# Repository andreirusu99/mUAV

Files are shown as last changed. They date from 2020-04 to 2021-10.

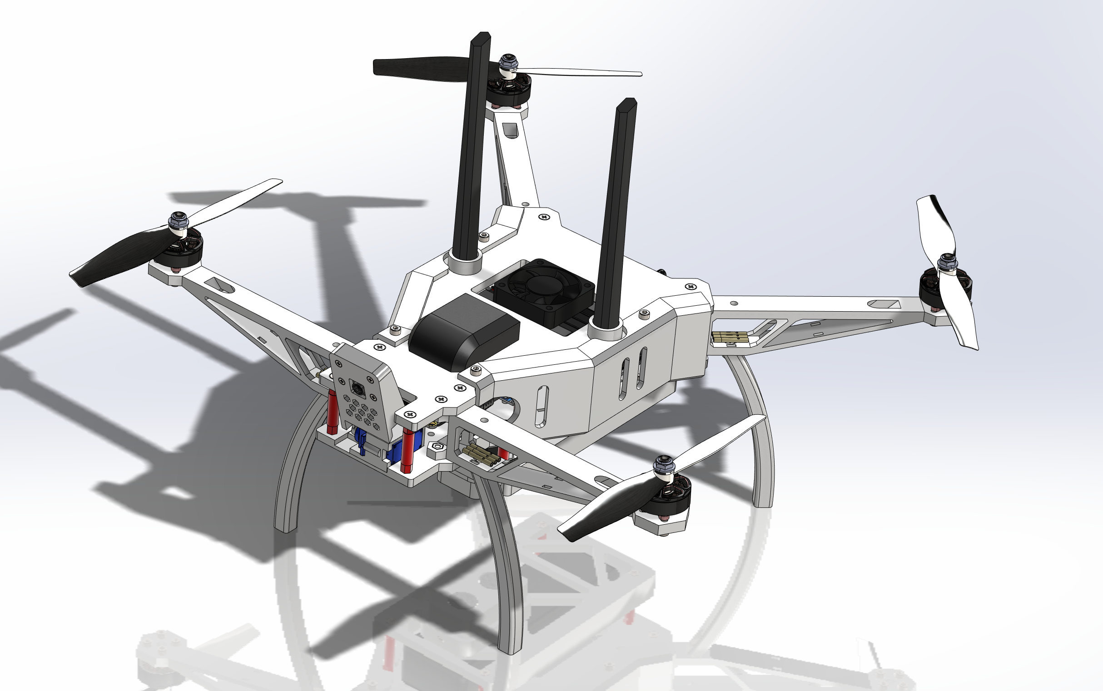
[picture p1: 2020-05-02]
Hardware/cad.png

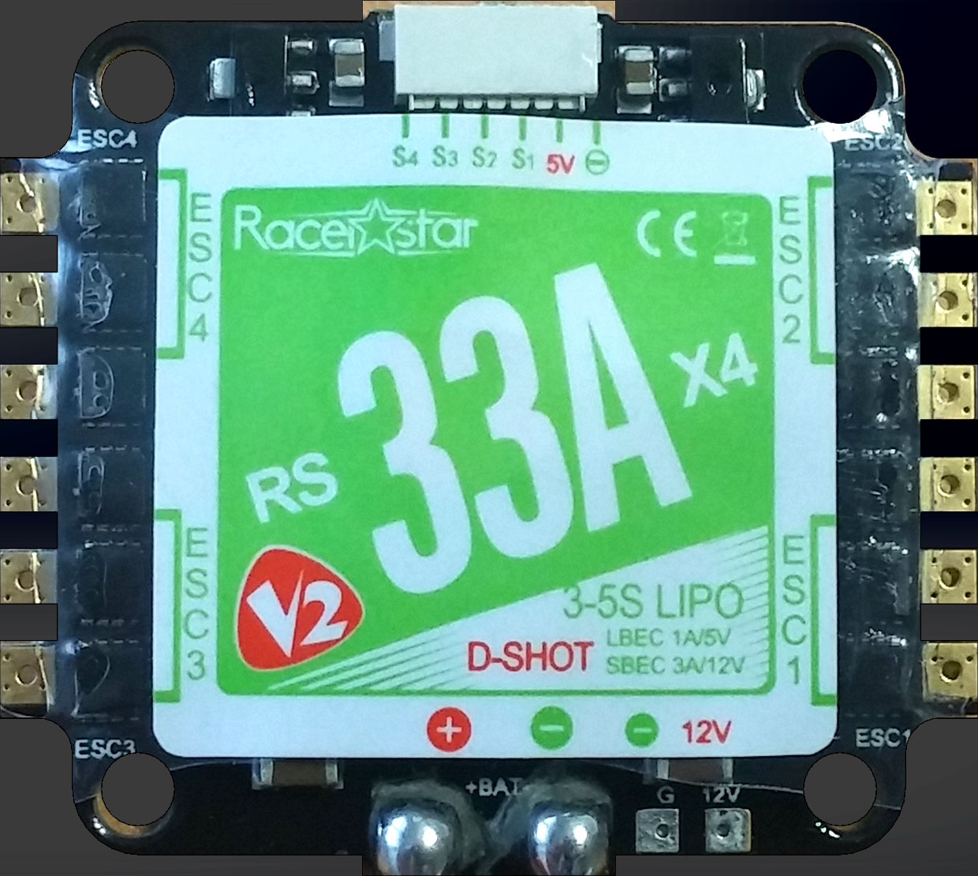
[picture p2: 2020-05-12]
Hardware/esc-racerstar-4in1-33a-v2-1.snapshot.1/TEXT_RACERSTAR_33A_TOP.jpg

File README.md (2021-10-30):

### ***This project represents the work for my bachelor's thesis and therefore, any commercial usage or distribution of the files without expressly granted written permission and consent is prohibited.***

Complete information in the [Thesis](/Thesis.pdf) document and the presentation (_Crowd identification and monitoring using UAVs.pdf_)

## Summary
Edge computing system for mUAV crowd identification and monitoring, complete with client application, real-time dashboard and statistics.

The purpouse of the project is to implement a crowd identification and monitoring system that runs on edge, on a drone that I designed and built (see *Hardware* folder for details).

Edge computing is done on a nVIDIA Jetson Nano Dev Kit installed on the quadcopter, that runs a ROS environment.

Crowd monitoring is performed using neural networks designed for edge devices (SSD MobileNet V2) and computer vision frameworks such as OpenCV.

The Jetson communicates completely wireless over a Wi-Fi hotspot from a computer (my laptop).

## Frameworks & APIs
- **ROS Melodic** (Robot Operating System), Python implementation
- **OpenCV 4.1.1**, built from source with CUDA support
- **TensorFlow 2**, for model tests
- **Flask Server**, for live video streaming
- **ReactJS**, for the front-end application
- **GoogleMapsAPI** for real-time GPS localization
- **ROSLibJS** for remote ROS topic access
- **YAMSPy** for MSP communication with the FC

## Folder Structure
### [catkin_ws](/catkin_ws)
Contains the ROS workspace, which constitutes the main functional part of the system. Inside, there are the source files of ROS Nodes, message definitions, and a launch file that launches all the required nodes. The programming language is Python, using the *rospy* library.

### [ros_client](/ros_client)
Contains a React application that uses ROSLibJS to interact with the Master Node running on the Jetson Nano, that displays real-time data in a dashboard by accessing the topics of the ROS runtime. 

### [GroundStation](/GroundStation)
Contains a Python script used to send UDP commands over Wi-Fi from a joystick connected to the ground computer (my laptop). The commands are sent as-is and all processing and interpretation of these commands is done in the air on the Jetson.
> Note: the drone's flight is not automated, therefore an operator is required for flying (flight automation was outside the scope of this project).

### [Hardware](/Hardware)
Contains the 3D models that make up the quadcopter. These parts were designed with 3D printing manufacturing in mind, and as such, are only suitable for this kind of manufacturing process. The parts were printed on my own 3D printer using PETG. and PLA. A detailed description of all the hardware components used (boards, sensors, actuators) is found in the Readme file inside the folder.

### [ModelTest](/ModelTest)
Is a folder that I created to host my neural network experiments, until I decied for the final implementation that I would transfer over to the Jetson for inferencing.

### Further information can be found in each respective folder.

## Helpful work by others
 - [DronePilot](https://github.com/alduxvm/DronePilot) - UDP joystick communication between computers
 - [YAMSPy](https://github.com/thecognifly/YAMSPy) - MSP library for Python
 - [Jetson Inference](https://github.com/dusty-nv/jetson-inference) - official deep learning inference library from nVidia

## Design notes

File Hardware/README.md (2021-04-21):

# Hardware

## Quadcopter
Designed with 3D printing and modularity in mind, it acts as an enclosure for all the other components. 
Designed in SolidWorks and sliced with Ultimaker Cura.

It features a 3-deck design, where in the middle deck lie the most important components (Jetson Nano, Flight Controller, Camera). 
The upper deck hosts the GPS and the Wi-Fi antennas, while the lower deck contains the LiPo battery, the sonar, and a servo release mechanism.

The front arms are pulled back (in comparison to a regular simmetrical quadcopter) in order for them not to interfere with the camera's image. The propellers are placed well above the center of gravity for increased stability.
Additionally, each motor is inclined by 3 degrees horizontally to further improve hover stability.

The entire craft is suspended on 4 independent legs that can be easily replaced.
The motor arms are also modular and can be easily replaced if broken.
The sides are covered for extra protection in case of falls.

Drone

## Main Computer
The nVidia Jetson Nano Developer Kit is used in this project, mainly due to the fact that it boasts a Maxwell GPU (alongside a 4 core ARM CPU) capable of fast deep-learning inference speeds.
Additionally, the wealth of expasion ports and headers helps in connecting sensors and building complex applications. 
The Jetson is improved by the addition of an Intel Wi-Fi card, in the dedicated E key slot under the Nano module. 
This card has 2 antennas, which come out of the top of the drone and give the nano very good wireless coverage.

Runs Tegra4Linux, a custom Linux distro specific to the Jetson platform.

Jetson Nano

## Flight Controller
This is the component that directly interacts with the motors. The FC contains 4 separates ESCs to control the 4 separate motors.
It also provides a pass-through interface to control the servo to which the camera is attached, for tilt action.
It receives MSP (MultiWii Serial Protocol) commands on separate channels and runs PID loops and stabilisation algorithms to keep the drone level.
Uses Betaflight firmware and has an integrated IMU with an accelerometer and gyroscope.
It is mounted in the head of the craft, behind the camera and the tilting servo.

Flight Controller

## Sensors

### Camera
The camera used in this project is the RasberryPi Camera V2, with up to 4K resolution at 30FPS. It gives out a decent image, and has very good support on the Jetson Nano.
It plugs into one of the CSI camera ports on the Jetson.

RPi Cam V2

### Sonar
I used a simple HC-SR04(P) ultrasonic sensor as a sonar to obtain altitude information. It is mounted on the underside of the craft, facing downwards.

Sonar

### Barometer
A Bosch BMP-280 barometric and temperature sensor is used for altitude information when the craft is out of the range of the sonar (about 4m from the ground).
Communication between it and the Jetson is done using I2C. It is mounted behind the FC, above a 5V power regulator.

BMP-280

### GPS
As GPS, a VK-162 is used. It provides simple USB interface access and has good accuracy and reliability. 
It can be seen mounted on the topmost part of the drone, for better location signal.

VK-162

## Actuators
### Camera tilt servo
The camera is mounted on a servo arm that allows its tilting from 0 to 90 degrees. This is a helpful feature to have when taking shots from above, and is commonly found on cinematic drones (although those have extra axes).

Servo tilt

### Servo release mechaism
Additionally, a servo release mechanism is mounted on the underside of the craft, next to the sonar. It allows the carrying of objects, with a theoretical max capacity of about 2kg, but this is not tested.
> Note: this feature is not used in the project, I might do something with it afterwards

Servo release

### Motors and Propellers
I used 4 Turnigy BLDC, 2600KV motors (common for medium-scale drones), together with 6040 propellers (6" long, 4" pitch), with a rated thrust of 800g each.

## Stats
- Mass without battery: **~850g**
- Mass with battery: **~1200g** (3S LiPo 5200mAh, 55Wh)
- Propeller span: **50cm**
- Height: **15cm** (without antennas)
- Power consumption: **~10W** idle, **~150W** hover + **~10W** JetsonNano
- Average flight time: **20 min**
> Power consumption and flight times depend heavily on external factors such as air temperature, wind, humidity.

## Extra Photos
### Top View
> Shows the upper deck, with the Jetson Nano's fan, the GPS module, the antennas and various other design elements

top

### Bottom View
> Shos the sonar, the servo release, and the battery cage.

bottom

### Back View
> Shows the I/O ports of the Jetson. Left USB is the Flight Controller, right USB is the GPS.

back

### Flight Controller and Camera Servo
> You can spot the ventilation cutouts and the M3 nut capture locations embedded in the 3D-printed plastic

front

### Internal View
> Not all components had been installed when this picture was taken.

internal

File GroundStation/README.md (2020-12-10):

# GroundStation

### Contains a single Python script used to stream joystick data to the Jetson Nano over an UDP WebSocket.

## Flow

- reads the joystick axes and buttons using the `pygame` library
- rounds the axes to 3 decimals
- sends the data using an UDP socket (`socket.SOCK_DGRAM`) 

#### The UDP send address (IP and Port) are configured to be on the local network of the Wi-Fi hotspot created by the laptop.

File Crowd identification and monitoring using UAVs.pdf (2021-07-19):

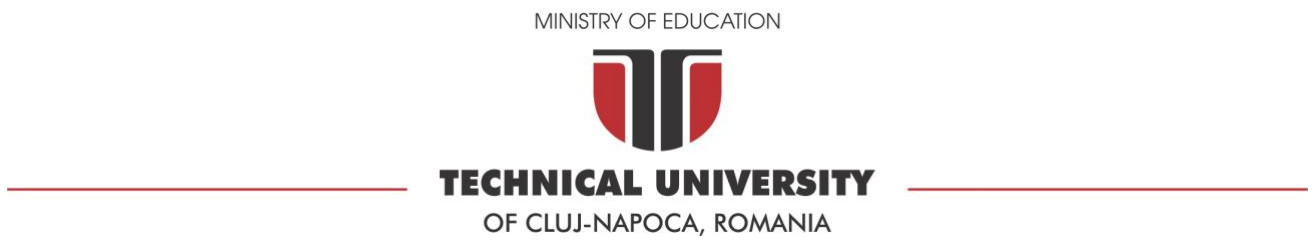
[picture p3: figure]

# Real-time crowd identification and monitoring using UAVs

# Student: Andrei Rusu

# Coordinator: Prof. Dr. Radu Dănescu

Technical University of Cluj-Napoca, Computer Science Department | 1

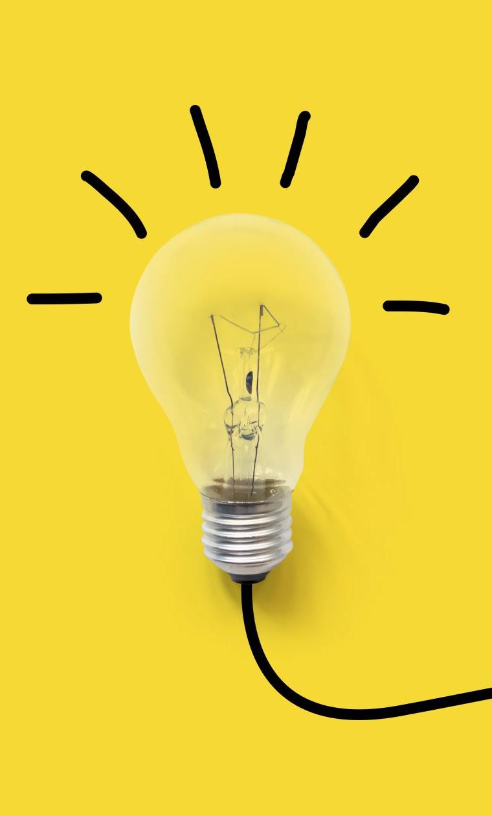
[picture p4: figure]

# Problem

# - Crowds in public places = large health hazard

# - Difficult to enforce social distancing

# - Traditional methods are slow and require offsite processing

Technical University of Cluj-Napoca, Computer Science Department | 2

# Objectives

# - Implement CV method for estimating overcrowding & social distancing

# - Leverage edge computing to enable real-time processing

# - Use UAVs for fast deployment anywhere

Technical University of Cluj-Napoca, Computer Science Department | 3

# Proposed solution

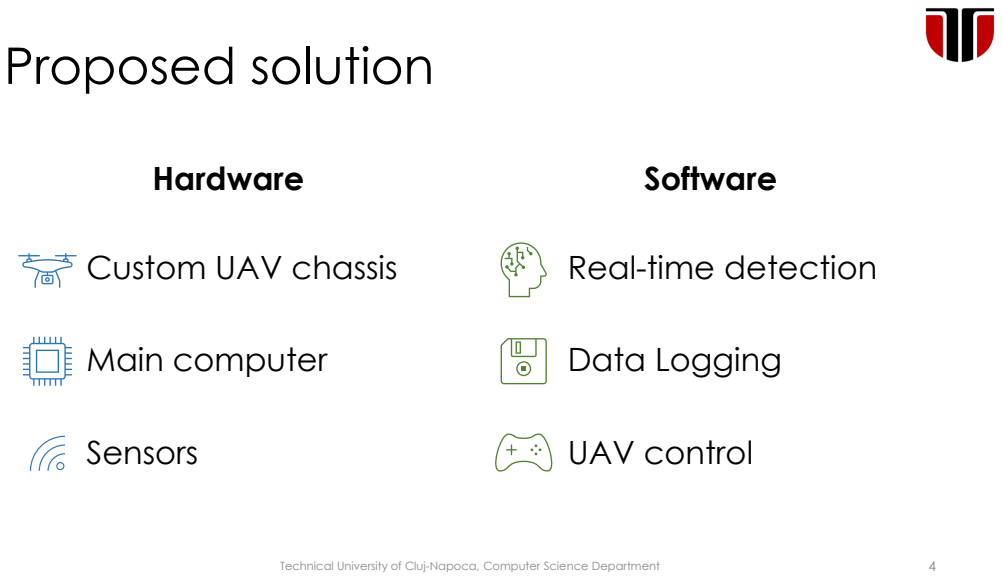
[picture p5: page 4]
Hardware; Main computer; Sensors; Software; Data Logging; UAV control; Technical University of Cluj-Napoca, Computer Science Department

Custom UAV chassis

Real-time detection

# Hardware platform

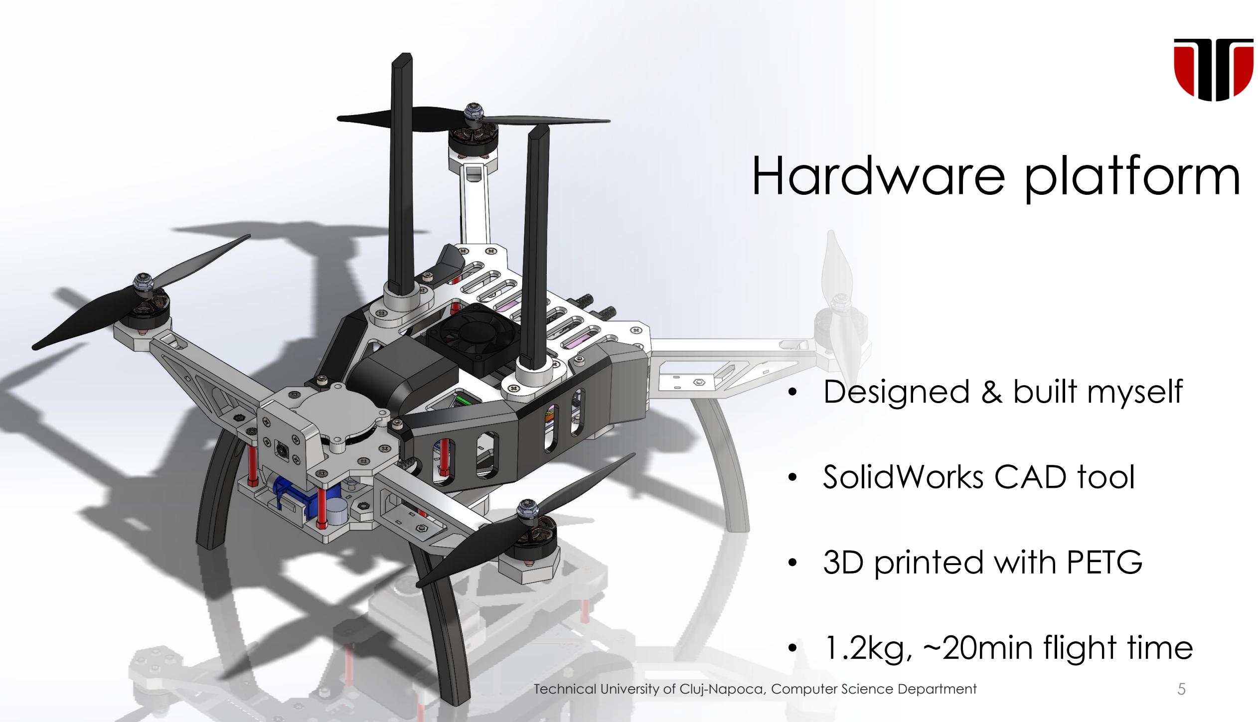
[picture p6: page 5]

# - Designed & built myself

# - SolidWorks CAD tool

# - 3D printed with PETG

# - 1.2kg, ~20min flight time

Technical University of Cluj-Napoca, Computer Science Department | 5

# Designed assemblies

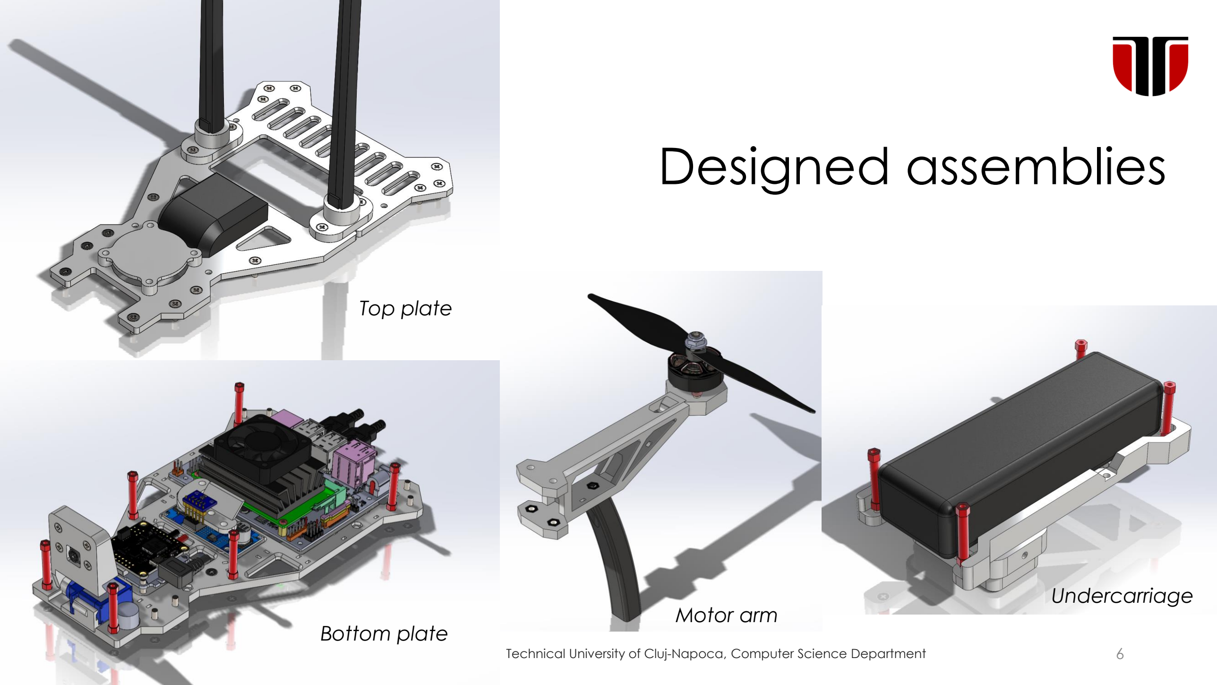
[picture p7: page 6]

## Bottom plate

## Top plate

## Motor arm

## Undercarriage

Technical University of Cluj-Napoca, Computer Science Department | 6

# Hardware components

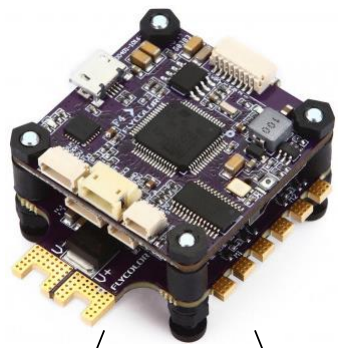
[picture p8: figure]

7

x4

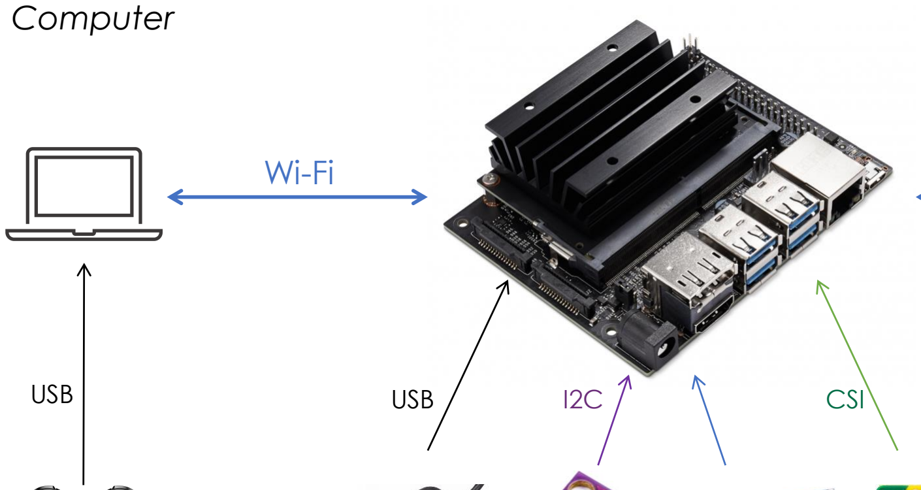
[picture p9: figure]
USB; CSI; Computer

GPS | Barometer | Sonar | Camera | Servo | Motors

# MSP

PWM | PWM

# Ground Station

NVidia Jetson Nano | Flight Controller

## Gamepad

Technical University of Cluj-Napoca, Computer Science Department

# Software components

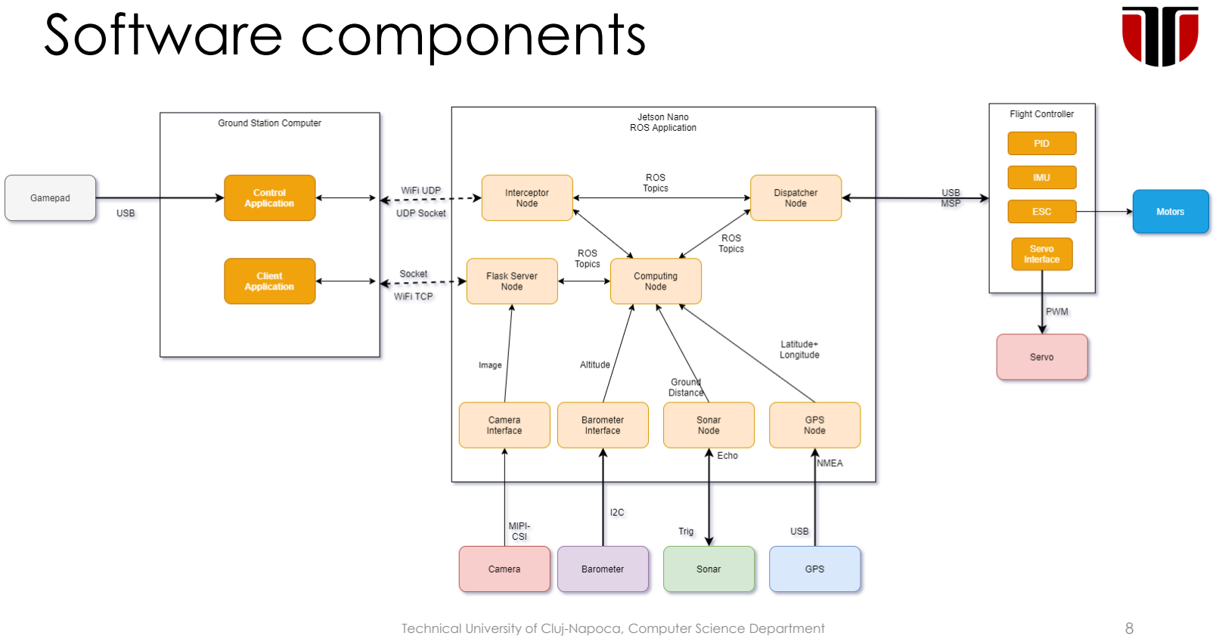
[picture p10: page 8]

Technical University of Cluj-Napoca, Computer Science Department | 8

# Application

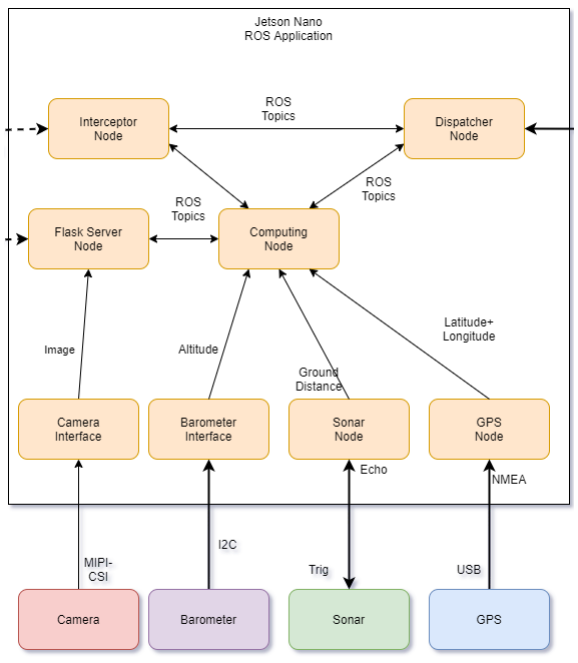
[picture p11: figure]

Technical University of Cluj-Napoca, Computer Science Department | 9

# - MobileNetV2 SSD for person detection

# - Overcrowding & social distancing

# - Data gathering & logging to .csv

# - Flight control via MSP

# Parallel execution

## runs on JetsonNano

# Person detection

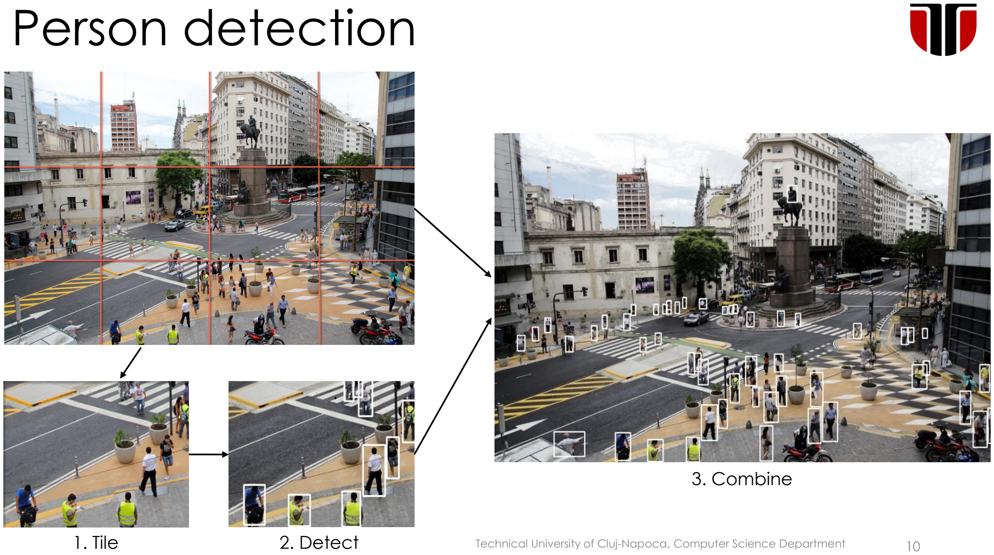
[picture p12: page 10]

1. Tile | 2. Detect | Technical University of Cluj-Napoca, Computer Science Department | 10

## 3. Combine

Technical University of Cluj-Napoca, Computer Science Department | 11

# - Density = Area / People

# - Obtain area of ground projection from H and αcam

# - Pixel size = Area / resolution [cm]

# - Distance on ground = Distance on image * pixel size

# Overcrowding & Social distancing

# Estimate distances between people

# Estimate average density of crowd

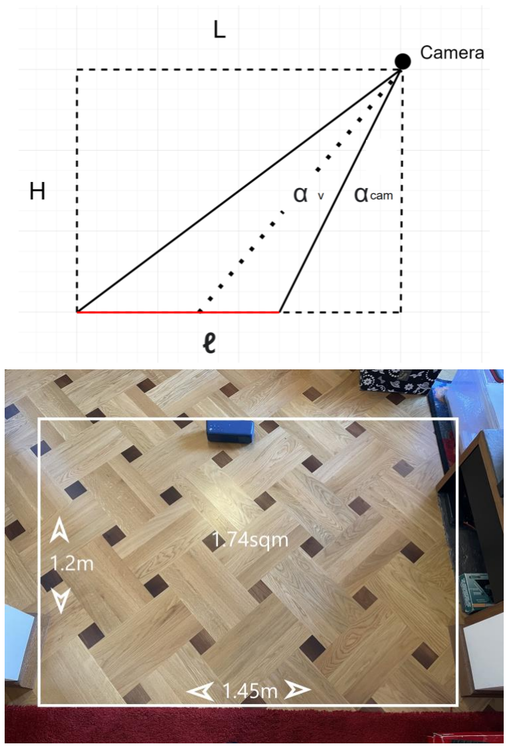
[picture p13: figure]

## Area estimation test

# Client Application

## runs on GS Computer

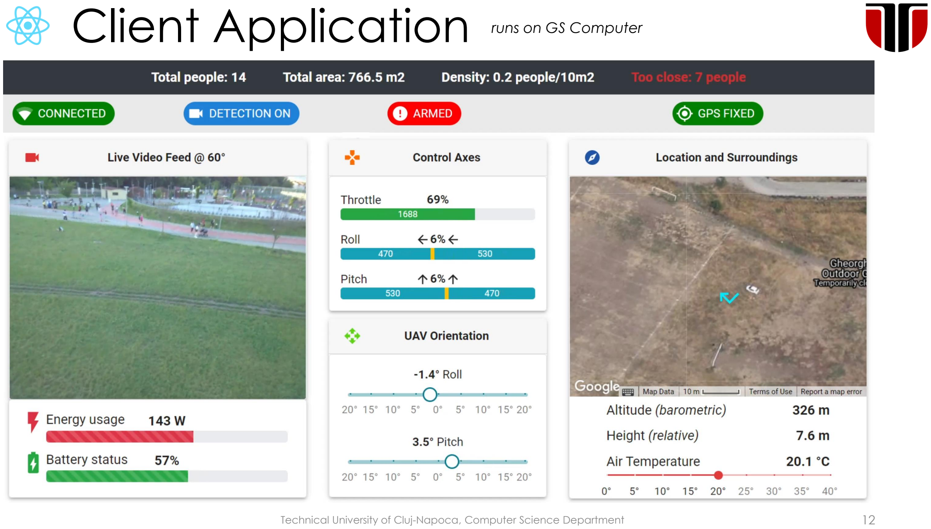
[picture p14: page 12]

Technical University of Cluj-Napoca, Computer Science Department | 12

# Control application

# - Sends UDP messages to the ROS application

# - Message:

# 4 control axes (Roll, Pitch, Throttle, Yaw) 2 triggers 6 buttons 1 Directional pad

# - Controls drone & functions

## (flying, camera tilt, detection etc.)

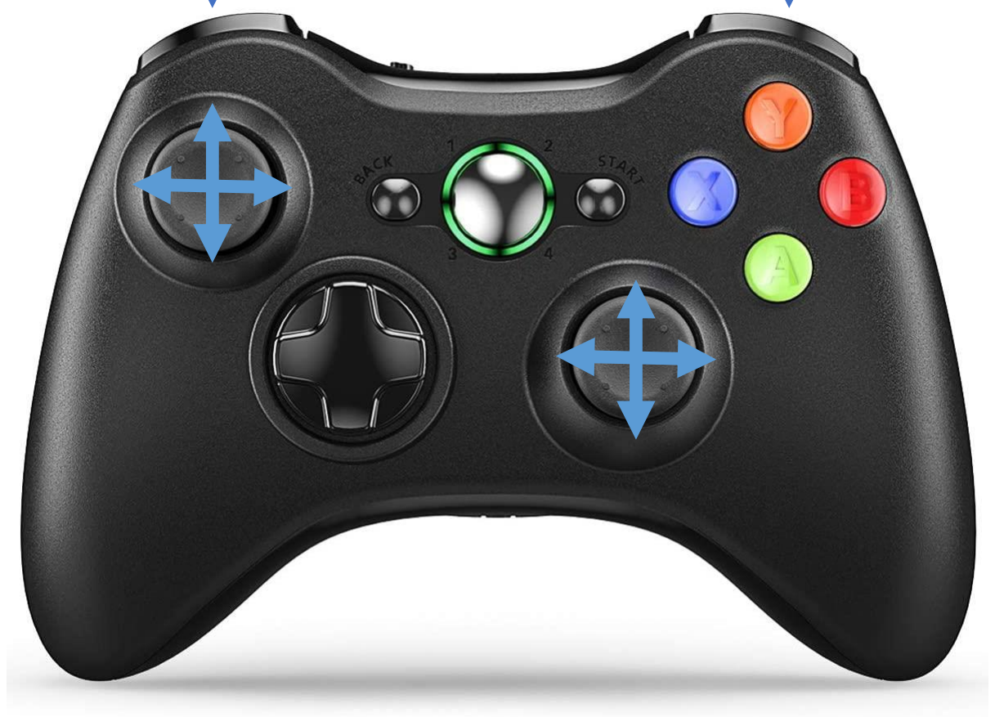
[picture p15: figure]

Technical University of Cluj-Napoca, Computer Science Department | 13

## runs on GS computer

# Validation

Board | CPU | TOPS | Interfaces | Speed | Weight | Cost | PricePerf
RPi4 | 4 | 0 | USB2+3,HDMI, UART, I2C, SPI | 483ms | 46g | $50 | 24,150
RPi4 + Coral | 4 | 4 | USB2+3, UART, I2C, SPI | 25ms | ~100g | $110 | 2750
Nano Jetson | 4 | 0.5 | USB3, DP, HDMI, UART, I2C, SPI | 25ms | 250g | $100 | 2500
Xavier Jetson | 6 | 21 | UART, I2C, SPI USB3, DP, HDMI, | 1.25ms | 400g | $400 | 500
Technical University of Cluj-Napoca, Computer Science Department | 14
N | M | Tile Width | Tile Height | Runtime/Tile | Runtime/Image | Correctness
3 | 2 | 544 | 616 | 50ms | 305ms | 65%
4 | 3 | 408 | 410 | 54ms | 650ms | 67%
5 | 4 | 326 | 308 | 45ms | 905ms | 73%
6 | 4 | 272 | 308 | 43ms | 1050ms | 76%
8 | 6 | 204 | 205 | 44ms | 2100ms | 67%

# Main computer comparison using MobileNetV2SSD inference speed

# Image tiling comparison for 1632x1232 input image

# Results

## Flight deployment at Baza Sportivă Gheorgheni

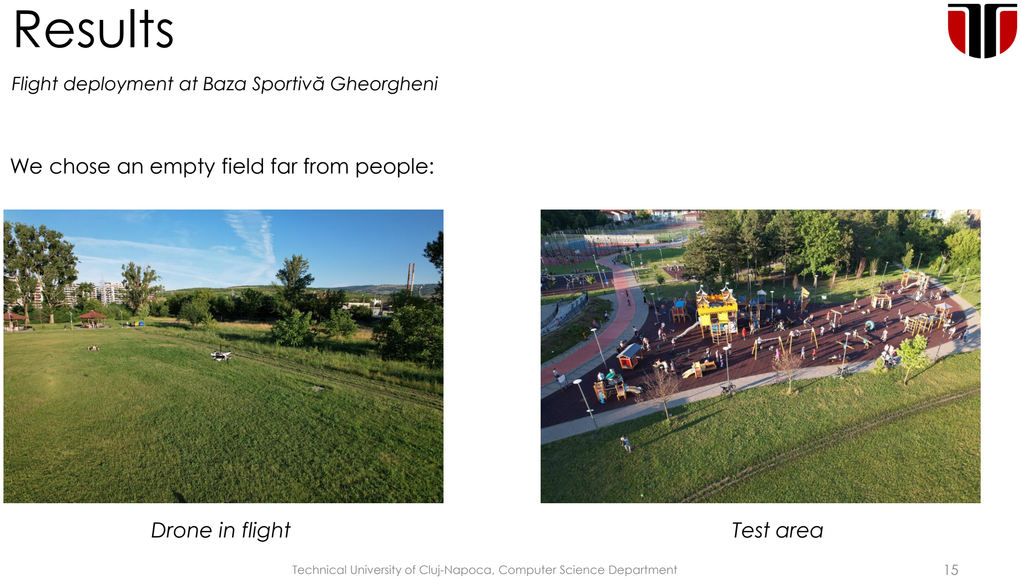
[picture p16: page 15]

Technical University of Cluj-Napoca, Computer Science Department | 15

# Drone in flight

# Test area

# We chose an empty field far from people:

# Results

16

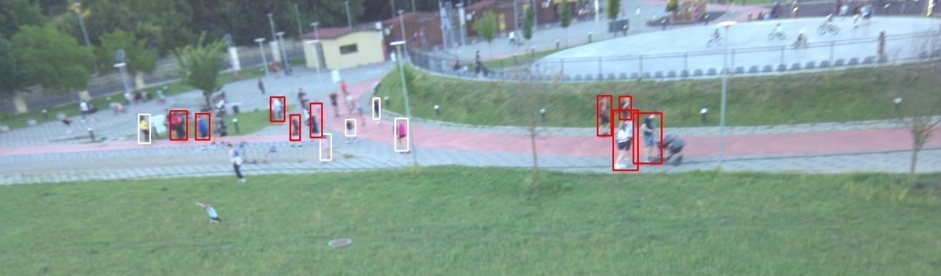
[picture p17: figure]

# 7.7m high, 60deg camera angle

# 14 of 23 people detected (60.8%)

# 9 too close, 0.18/10m2 density in 1340m2

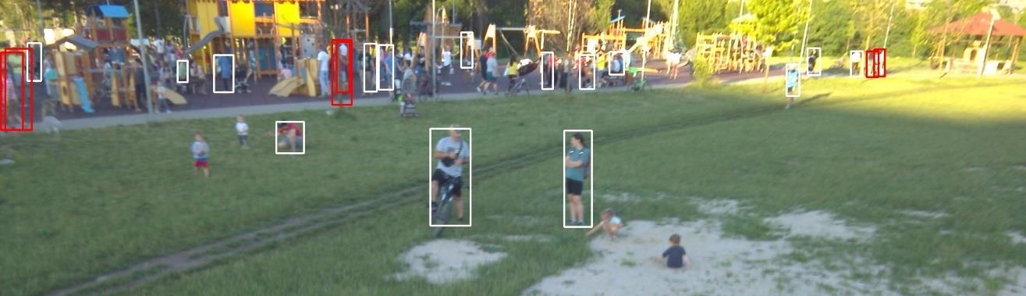
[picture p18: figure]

Technical University of Cluj-Napoca, Computer Science Department

# 3.2m high, 65deg camera angle

# 21 of 32 people detected (65.6%) 6 too close, 0.16/10m2 density in 786m2

## Flight deployment at Baza Sportivă Gheorgheni

# Complete system for crowd identification and

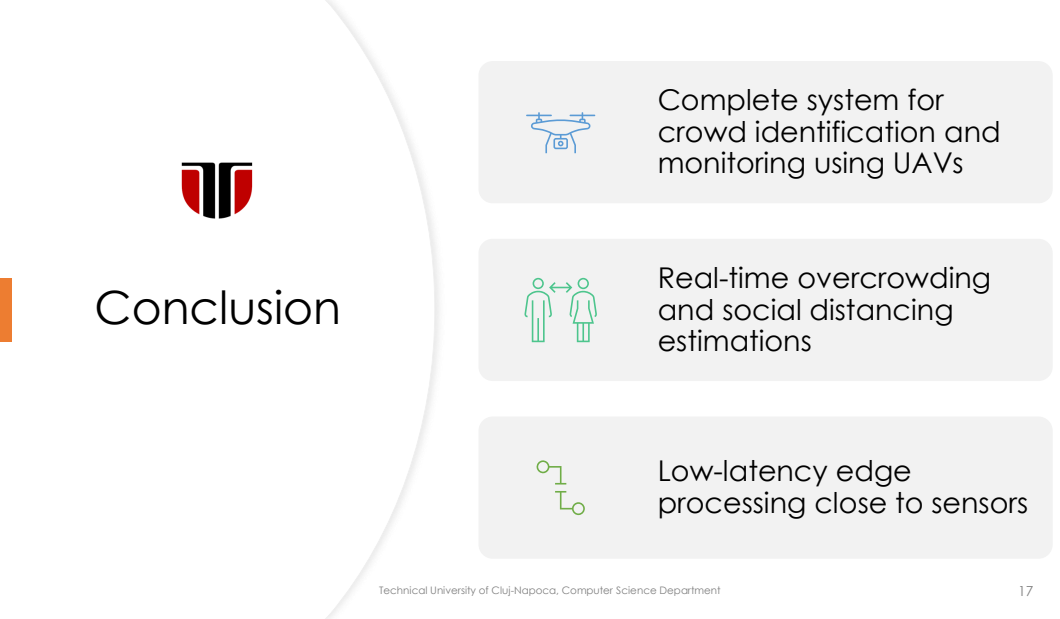
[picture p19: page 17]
Conclusion; Technical University of Cluj-Napoca, Computer Science Department

monitoring using UAVs

Real-time overcrowding
and social distancing
estimations

Low-latency edge
processing close to sensors

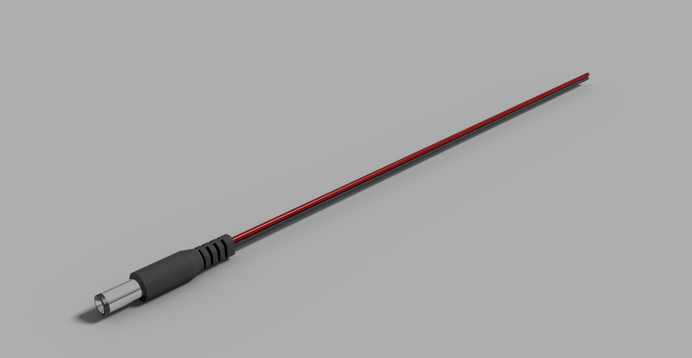
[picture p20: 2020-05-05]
Hardware/2-1-x-5-5-mm-barrel-connector-male-1.snapshot.1/2.1x5.5mm Barrel Connector Male.jpg

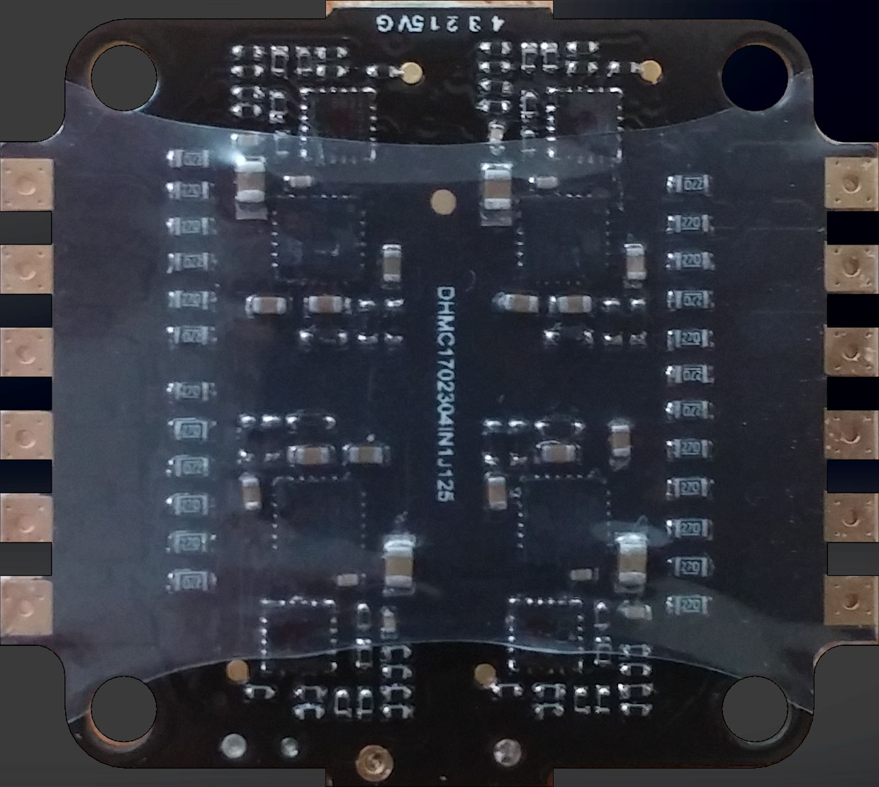
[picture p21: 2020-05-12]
Hardware/esc-racerstar-4in1-33a-v2-1.snapshot.1/TEXT_RACERSTAR_33A_BOTTOM.jpg

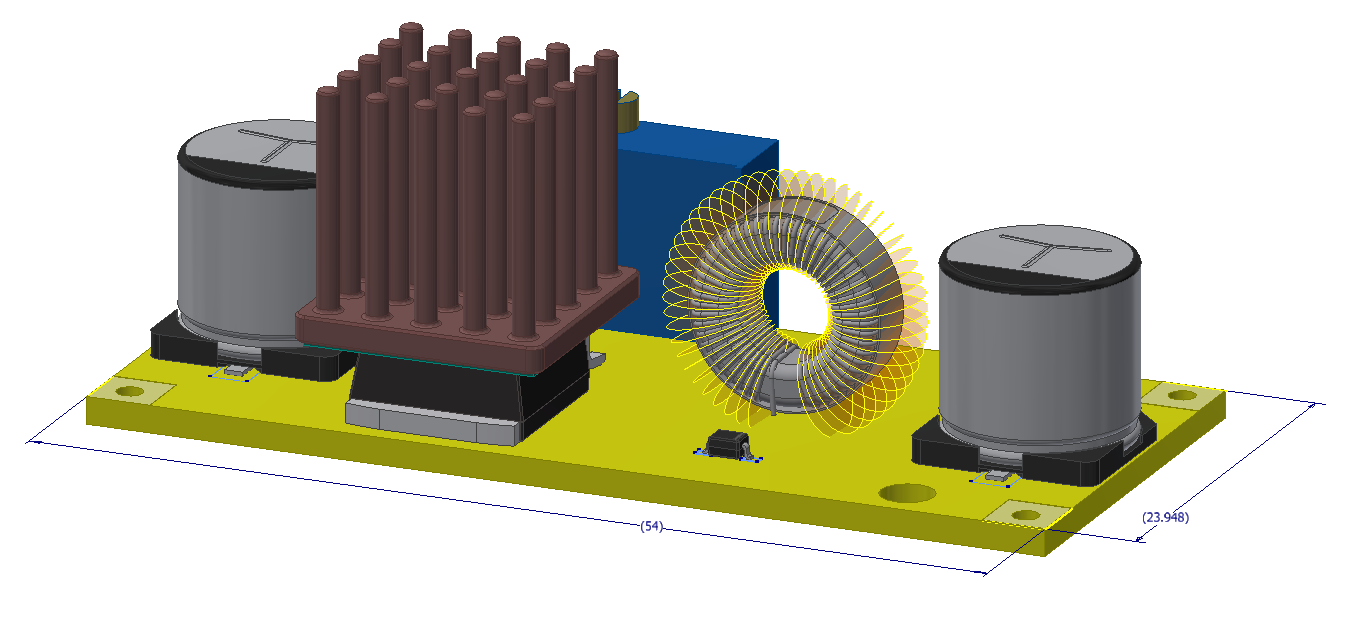
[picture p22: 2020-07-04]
Hardware/xl4015-dc-dc-stepdown-converter-1.snapshot.1/XL4015 DC-DC.png

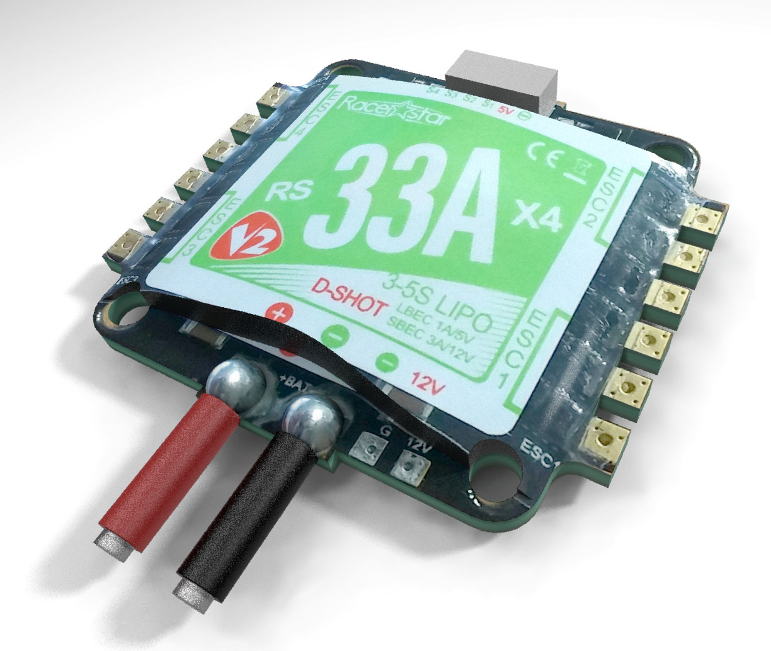
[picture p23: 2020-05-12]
Hardware/esc-racerstar-4in1-33a-v2-1.snapshot.1/RACERSTAR_33A_V2_RENDER.jpg

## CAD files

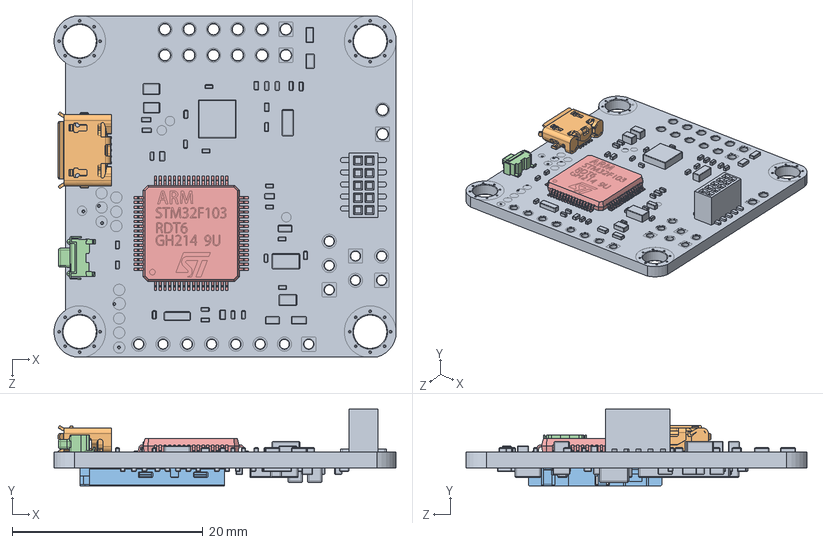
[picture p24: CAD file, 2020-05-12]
Hardware/hobbywing-x-rotor-f4-flight-controller-1.snapshot.1/Hobbywing Xrotor F4 FC.SLDASM
35.9 x 8.05 x 35.8 mm
MOTHER BOARD
USB port
microSD slot
Tact SMD Corner SWITRONIC IT-1100
STM32F103RDT6

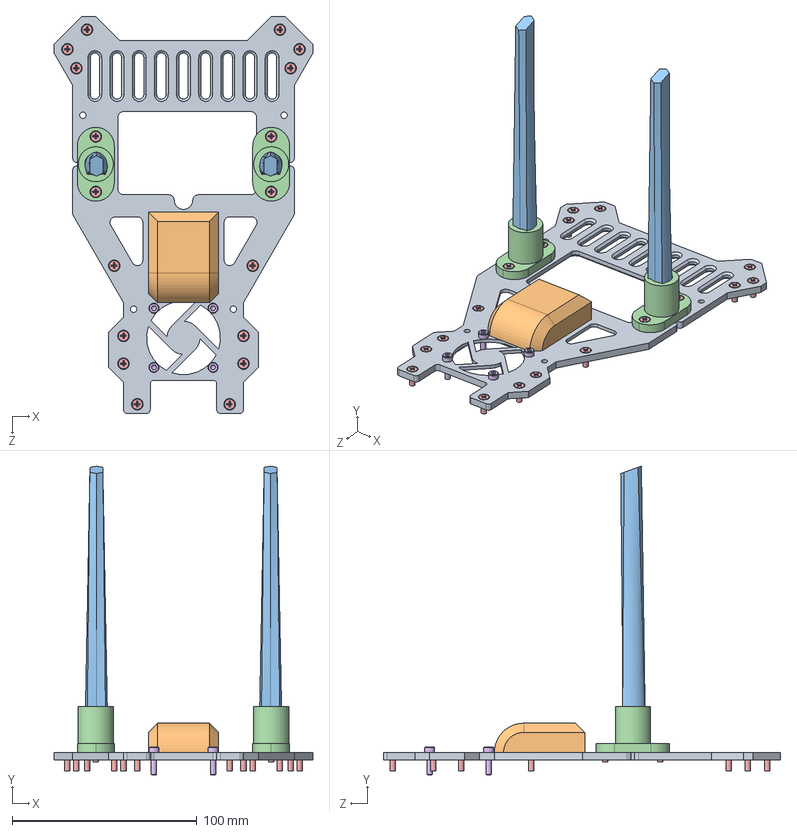
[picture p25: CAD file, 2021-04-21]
Hardware/Top Chassis ASM.SLDASM
140.0 x 167.2 x 215.0 mm
Top Chassis
Vk-162 GPS
ASUS Wireless USB AC56 Antenna x 2
Antenna Mount x 2
flat head screw_am x 18
socket head cap screw_am x 4

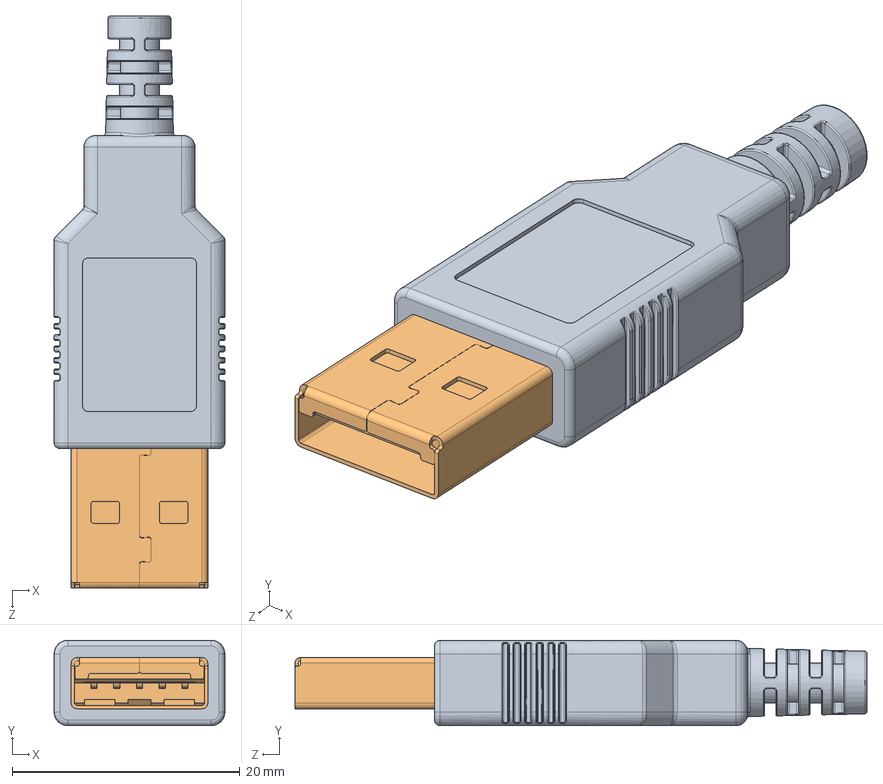
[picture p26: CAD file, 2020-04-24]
Hardware/usb-a-plug-1.snapshot.6/USB A Plug.SLDASM
15.0 x 7.50 x 50.3 mm
USB_Plastic.step
USB-Front.step

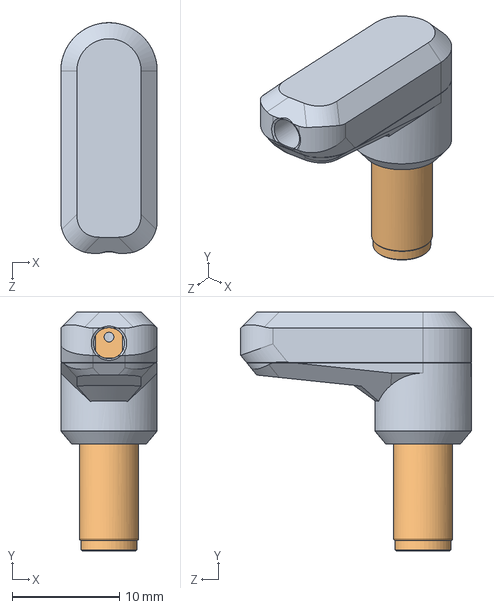
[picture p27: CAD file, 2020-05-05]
Hardware/case-for-power-jack-5-5-x-2-1-or-5-5-x-2-5-mm-1.snapshot.2/Сборка.SLDASM
9.00 x 22.3 x 21.5 mm
Корпус
Штирь

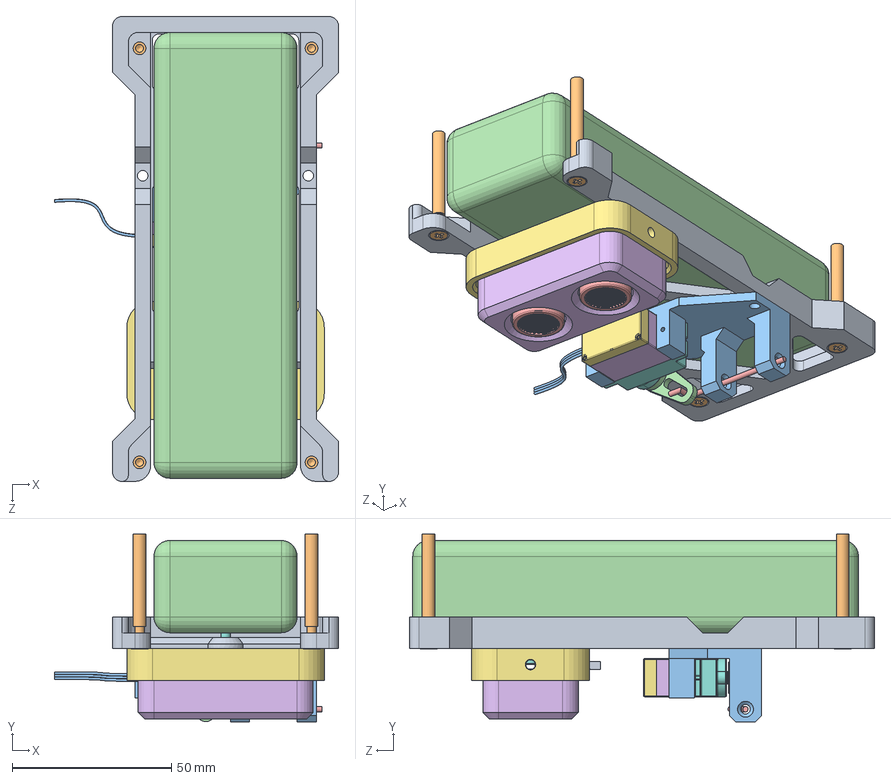
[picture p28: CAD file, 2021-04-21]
Hardware/Undercarriage ASM.SLDASM
89.2 x 59.0 x 146.0 mm
Battery Case
ALU spacer x 4
M3 Nut
3S 5.2Ah LiPo
HC-SR04-UltrasonicSensor v7
Sonar Housing
Sonar Housing Mount
socket head cap screw_am
DS1071-1x4
flat head screw_am x 4
Release Mechanism Servo Mount
Servo Arm
Release Rod
Servo HXT900 Micro - Carca_a Intermedi_ria.STEP
Servo HXT900 Micro - Carca_a Inferior.STEP
Servo HXT900 Micro - Carca_a Superior.STEP
Servo HXT900 Micro - Engrenagem Superior.STEP
Pe_a7^Servo HXT900 Micro.STEP

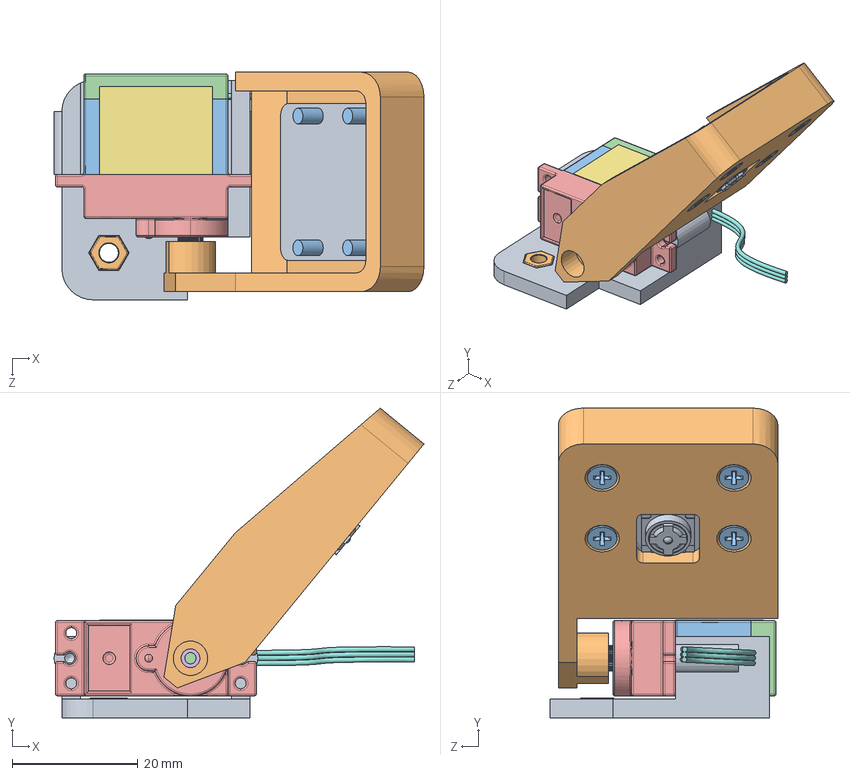
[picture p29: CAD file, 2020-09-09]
Hardware/Camera ASM.SLDASM
59.0 x 49.4 x 36.3 mm
PiCam V2.1 v1
Camera Mount
Servo HXT900 Micro - Carca_a Intermedi_ria.STEP
Servo HXT900 Micro - Carca_a Inferior.STEP
Servo HXT900 Micro - Carca_a Superior.STEP
Servo HXT900 Micro - Engrenagem Superior.STEP
Pe_a7^Servo HXT900 Micro.STEP
Servo Mount
M3 Nut
flat head screw_am x 4

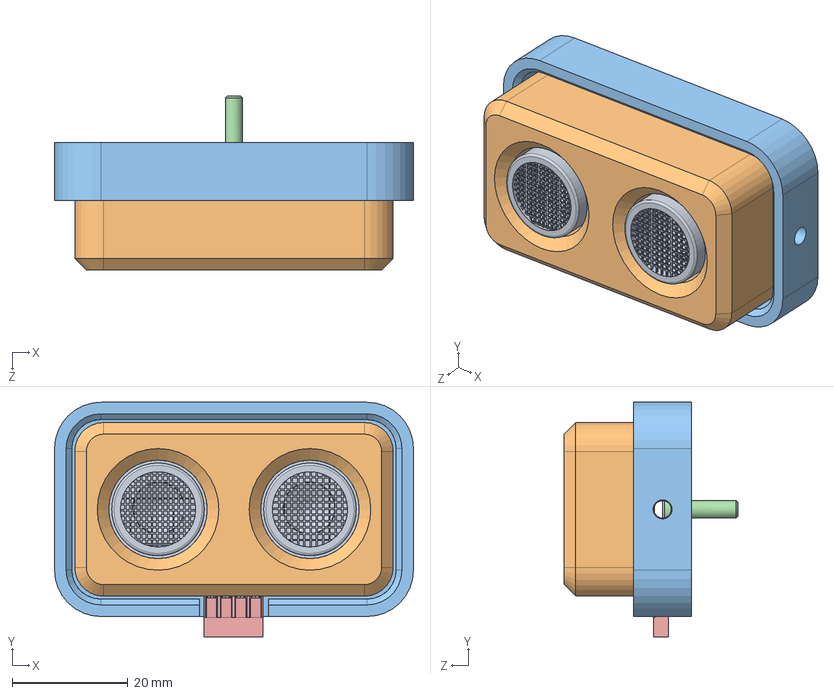
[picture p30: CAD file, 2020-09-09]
Hardware/Sonar ASM.SLDASM
62.0 x 40.5 x 30.0 mm
HC-SR04-UltrasonicSensor v7
Sonar Housing
Sonar Housing Mount
socket head cap screw_am
DS1071-1x4

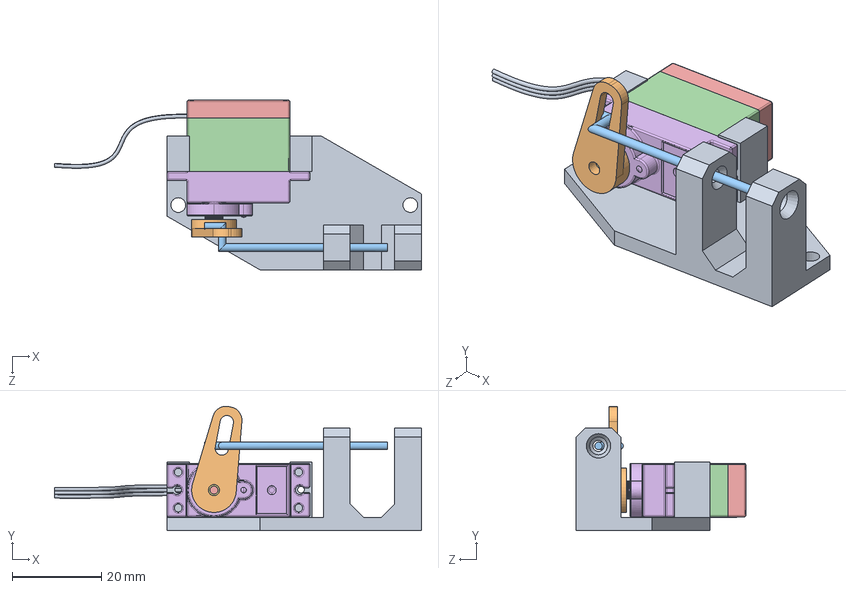
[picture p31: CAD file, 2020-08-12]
Hardware/Release Mechanism.SLDASM
82.2 x 27.9 x 38.0 mm
Release Mechanism Servo Mount
Servo Arm
Release Rod
Servo HXT900 Micro - Carca_a Intermedi_ria.STEP
Servo HXT900 Micro - Carca_a Inferior.STEP
Servo HXT900 Micro - Carca_a Superior.STEP
Servo HXT900 Micro - Engrenagem Superior.STEP
Pe_a7^Servo HXT900 Micro.STEP

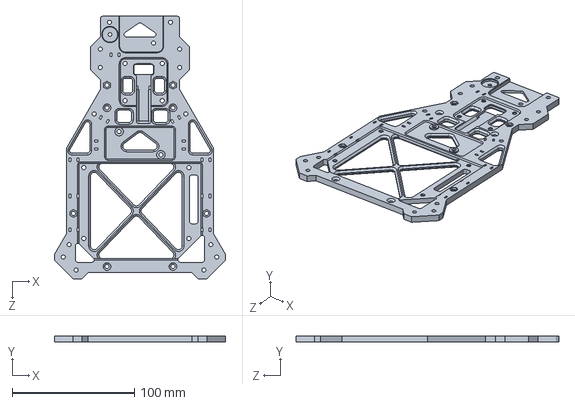
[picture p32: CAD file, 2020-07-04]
Hardware/Main Chassis.SLDPRT
140.0 x 5.00 x 215.0 mm

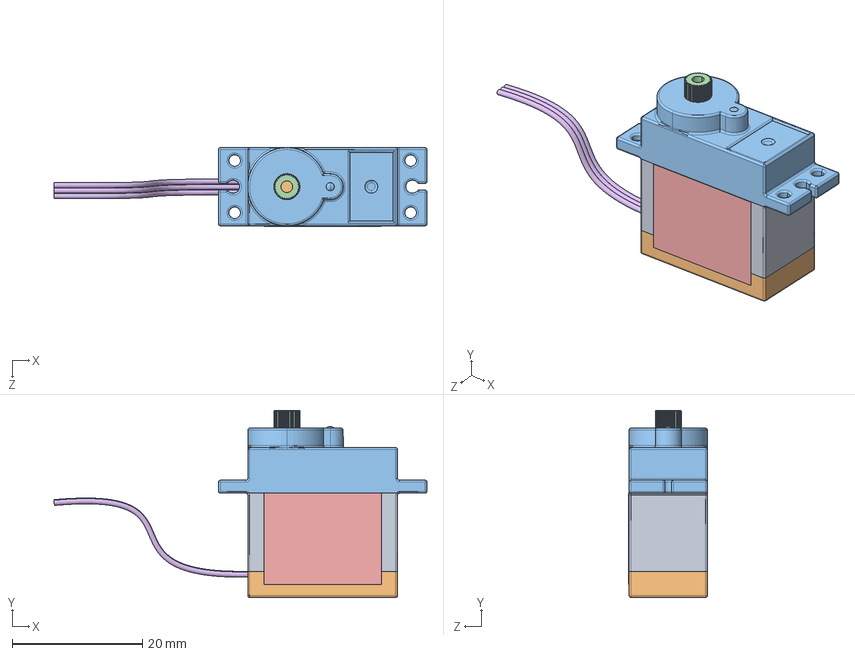
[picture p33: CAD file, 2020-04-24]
Hardware/Servo HXT900 Micro.SLDASM
57.2 x 28.7 x 12.1 mm
Servo HXT900 Micro - Carca_a Intermedi_ria.STEP
Servo HXT900 Micro - Carca_a Inferior.STEP
Servo HXT900 Micro - Carca_a Superior.STEP
Servo HXT900 Micro - Engrenagem Superior.STEP
Pe_a7^Servo HXT900 Micro.STEP

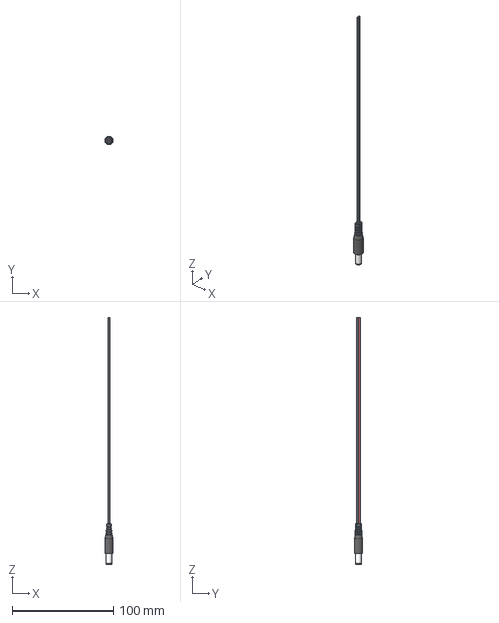
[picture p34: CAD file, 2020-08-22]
Hardware/2-1-x-5-5-mm-barrel-connector-male-1.snapshot.1/Male 2.1mm Barrel Jack.stp
8.24 x 8.25 x 243.5 mm

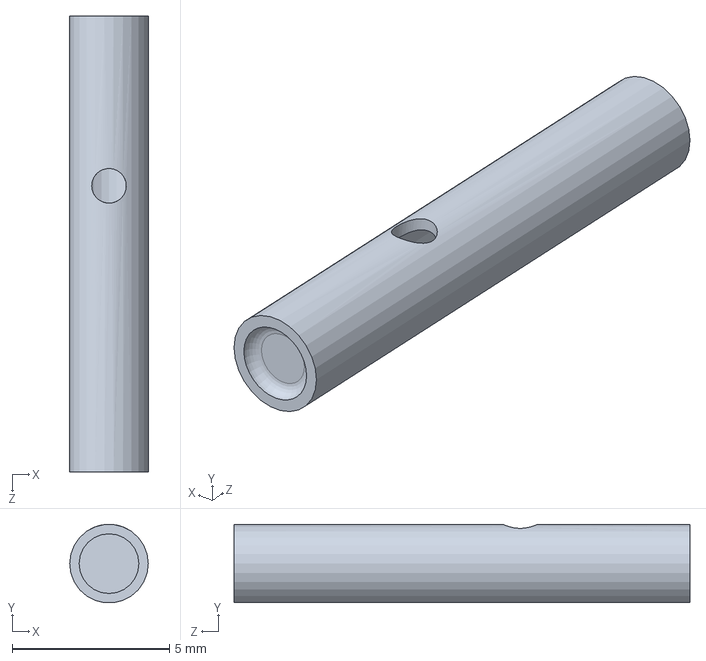
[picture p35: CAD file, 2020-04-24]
Hardware/2mm-bullet-plug-banana-connector-female-1.snapshot.2/Pin_PCB-Female.SLDPRT
2.50 x 2.49 x 14.5 mm

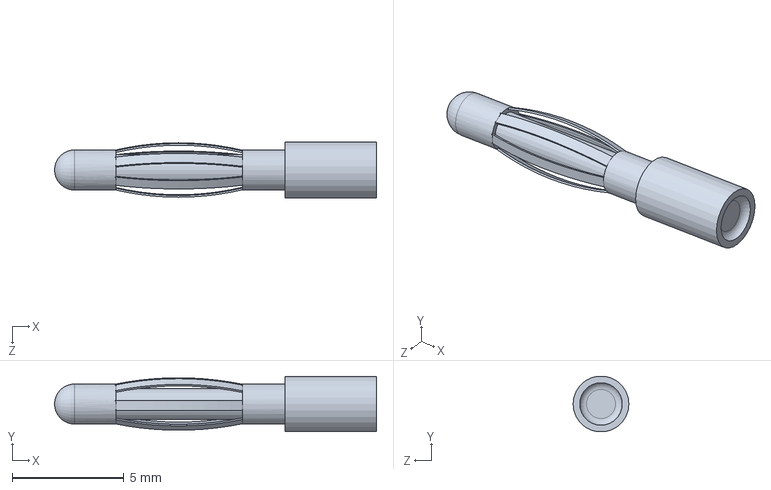
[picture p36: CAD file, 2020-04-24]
Hardware/2mm-bullet-plug-banana-connector-male-1.snapshot.5/Pin_PCB-Male.SLDPRT
14.4 x 2.48 x 2.50 mm

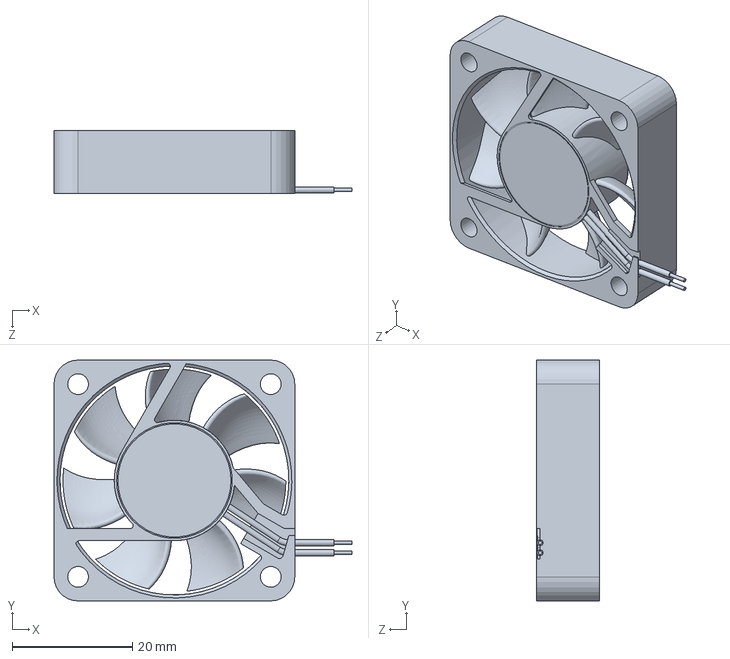
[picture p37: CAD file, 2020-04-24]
Hardware/40mm-dc-fan-1.snapshot.7/40x40x10 DC Fan.SLDPRT
49.5 x 40.0 x 10.5 mm

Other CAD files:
Hardware/asus-usb-ac56-wifi-dongle-1.snapshot.1/SolidWorks/ASUS Wireless USB AC56 Antenna.SLDPRT
Hardware/bmp280-module-1.snapshot.1/bmp280_module.SLDPRT
Hardware/case-for-power-jack-5-5-x-2-1-or-5-5-x-2-5-mm-1.snapshot.2/Корпус.SLDPRT
Hardware/dupont-cable-connector-2-54-mm-pitch-1.snapshot.6/DS1071-1xN (BLS)/DS1071-1x4.SLDPRT
Hardware/2-1-x-5-5-mm-barrel-connector-male-1.snapshot.1/Male 2.1mm Barrel Jack.SLDPRT
Hardware/2-1-x-5-5-mm-barrel-connector-male-1.snapshot.1/Male 2.1mm Barrel Jack.ipt
Hardware/3S 5.2Ah LiPo.SLDPRT
Hardware/ALU spacer.SLDPRT
Hardware/Antenna Mount.SLDPRT
Hardware/Arm - Angled.SLDPRT
Hardware/BMP Mount.SLDPRT
Hardware/Battery Case.SLDPRT
Hardware/Buzzer.SLDPRT
Hardware/Camera Mount.SLDPRT
Hardware/Front Opening Cover.SLDPRT
Hardware/HC-SR04-UltrasonicSensor v7.SLDPRT
Hardware/Leg Long.SLDPRT
Hardware/M3 Nut.SLDPRT
Hardware/PiCam V2.1 v1.SLDPRT
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

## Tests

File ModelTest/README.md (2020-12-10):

# ModelTest

#### A sandbox where I tested several object detecion models and where I test some other parts of the algorithm.

#### [src](/src) contains the Python scripts
#### [data](/data) contains test images
#### [results](/results) contains some results that I obtained
> Note: the data results folder are usually not the latest, since I do most of the testing on the Jetson directly

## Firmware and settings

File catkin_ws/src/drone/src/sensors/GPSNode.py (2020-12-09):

#!/usr/bin/env python3

import time

import numpy as np
import rospy
import serial
from drone.msg import GPSinfo as GPSMsg

fix_quality = 0
gps_time = ""  # UTC
latitude = 0.0  # N
longitude = 0.0  # E
ground_speed = 0.0  # km/h


def readString(ser):
    while True:
        while ser.read().decode("utf-8") != '$':  # Wait for the begging of the string
            pass  # Do nothing
        line = ser.readline().decode("utf-8")  # Read the entire string
        return line


def getTime(string, format, returnFormat):
    global gps_time
    # Convert date and time to a nice printable format
    gps_time = time.strftime(returnFormat, time.strptime(string, format))


def getLatLng(latString, lngString):
    if len(latString) > 0 and len(lngString) > 0:
        latString = latString[:2].lstrip(
            '0') + "." + "%.7s" % str(float(latString[2:]) * 1.0 / 60.0).lstrip("0.")
        lngString = lngString[:3].lstrip(
            '0') + "." + "%.7s" % str(float(lngString[3:]) * 1.0 / 60.0).lstrip("0.")
        return latString, lngString


def processRMC(lines):
    global latitude, longitude
    getTime(lines[1] + lines[9], "%H%M%S.%f%d%m%y", "%a %b %d %H:%M:%S %Y")
    latlng = getLatLng(lines[3], lines[5])
    latitude = latlng[0]
    longitude = latlng[1]


def processGGA(lines):
    global latitude, longitude, fix_quality
    getTime(lines[1], "%H%M%S.%f", "%H:%M:%S")
    latlng = getLatLng(lines[2], lines[4])
    latitude = latlng[0]
    longitude = latlng[1]
    if len(lines[6]) > 0:
        fix_quality = lines[6]


def processGLL(lines):
    global latitude, longitude
    getTime(lines[5], "%H%M%S.%f", "%H:%M:%S")
    latlng = getLatLng(lines[1], lines[3])
    latitude = latlng[0]
    longitude = latlng[1]


def processVTG(lines):
    global ground_speed
    if len(lines[7]) > 0:
        ground_speed = lines[7]


def main(ser):
    global latitude, longitude, ground_speed, fix_quality
    rospy.init_node('GPSNode')

    gps_pub = rospy.Publisher('GPS', GPSMsg, queue_size=1)

    rate = rospy.Rate(1)
    it = 0
    ring = 5
    speeds = [0.0] * ring
    fixed = False
    while not rospy.is_shutdown():

        line = readString(ser)
        lines = line.split(",")

        try:
            if lines[0] == "GPRMC":
                processRMC(lines)

            elif lines[0] == "GPGGA":
                processGGA(lines)

            elif lines[0] == "GPGLL":
                processGLL(lines)

            elif lines[0] == "GPVTG":
                processVTG(lines)

            fix_quality = int(fix_quality)

            if fix_quality > 0:

                if not fixed:
                    rospy.loginfo("{}: Fix gained with {} sat".format(rospy.get_caller_id(), fix_quality))
                    fixed = True

                latitude = float(latitude)
                longitude = float(longitude)
                ground_speed = round(float(ground_speed), 1)

                if ground_speed < 10:
                    ground_speed = 0

                it += 1
                it %= ring

                speeds[it] = ground_speed

                speeds_sorted = np.sort(speeds)

                spd = round(speeds_sorted[ring // 2])

                gps_pub.publish(GPSMsg(latitude, longitude, spd, fix_quality))

            else:
                if fixed:
                    rospy.loginfo("{}: Fix Lost!".format(rospy.get_caller_id()))
                    fixed = False

            rate.sleep()

        except Exception as e:
            # rospy.logerr("{}: {}".format(rospy.get_caller_id(), e))
            pass


if __name__ == '__main__':

    try:

        serial_port = '/dev/' + rospy.get_param("/serial/gps_vk")
        ser = serial.Serial(serial_port, 9600, timeout=1)

        main(ser)

    except rospy.ROSInterruptException as error:
        pass

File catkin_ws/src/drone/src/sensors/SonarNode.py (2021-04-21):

#!/usr/bin/env python3

import time

import Jetson.GPIO as GPIO
import numpy as np
import rospy
from std_msgs.msg import Float32 as SonarMsg

TRIG = 27
ECHO = 17


def reading():
    GPIO.output(TRIG, False)
    time.sleep(0.01)

    # set Trigger to HIGH
    GPIO.output(TRIG, True)

    # set Trigger after 0.02ms to LOW
    time.sleep(0.00002)
    GPIO.output(TRIG, False)

    pulse_start = time.time()

    maxTime = 0.02
    timeout = pulse_start + maxTime

    while GPIO.input(ECHO) == 0 and pulse_start < timeout:
        pulse_start = time.time()

    if pulse_start >= timeout:
        return 0.0

    pulse_end = time.time()
    timeout = pulse_end + maxTime

    while GPIO.input(ECHO) == 1 and pulse_end < timeout:
        pulse_end = time.time()

    if pulse_end >= timeout:
        return 0.0

    pulse_duration = pulse_end - pulse_start
    distance = pulse_duration * 17150

    return distance


def main():
    rospy.init_node('SonarNode')

    pub = rospy.Publisher('SonarReading', SonarMsg, queue_size=1)

    # GPIO Mode (BOARD / BCM)
    GPIO.setmode(GPIO.BCM)
    GPIO.setwarnings(False)

    # set GPIO direction (IN / OUT)
    GPIO.setup(TRIG, GPIO.OUT)
    GPIO.setup(ECHO, GPIO.IN)

    it = 0
    ring = 10
    distances = [0.0] * ring
    rate = rospy.Rate(15)  # Hz
    last_pub = 0
    pub_hz = 5
    pub_rate = 1.0 / pub_hz
    while not rospy.is_shutdown():
        it += 1
        it %= ring
        distances[it] = reading()

        # invalid reading
        if distances[it] < 2:
            distances[it] = 0

        distances = np.sort(distances)
        distance = round(distances[ring // 2])

        if time.time() - last_pub > pub_rate:
            # rospy.loginfo("{}: {}cm".format(rospy.get_caller_id(), distance))
            pub.publish(SonarMsg(distance))
            last_pub = time.time()

        rate.sleep()


if __name__ == "__main__":

    try:
        main()

    except rospy.ROSInterruptException as error:
        pass

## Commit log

2020-04-26 Modified files.
    [032-0256-000_1.ipt, 0402_H040.ipt, 0402_H060.ipt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]
2020-04-26 Added the hardware files
    [032-0256-000_1.ipt, 0402_H040.ipt, 0402_H060.ipt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]
2020-04-27 Removed unrequired files from Hardware
    [Arm.STL, BPTT_slungload_test.csv, Leg Long.STL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]
2020-05-02 Removed unnecesary components, refactored others.
    [032-0256-000_1.ipt, 0402_H040.ipt, 0402_H060.ipt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]
2020-05-05 Replaced the M2 screws with M2.5 ones. Added an M2.5 captured nut to the sonar housing. Changed the top antenna mounts to allow 3D printing the top chassis with the top side down for better visuals.
    [Camera ASM.SLDASM, Camera Mount.SLDPRT, Main Chassis.SLDPRT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]
2020-05-05 Removed the redundant Router, moved its current functionalities to the Dispatcher. Refactored variables to signal that they should not be externally modified.
2020-05-06 Added the initial code for the Pilot. Added initial code for the GPS, Barometer and Sonar interfaces (not tested). Implemented functions to receive attitude info from the drone.
2020-05-12 Refactored the battery case. Reduced the length of the motor arm. Increased the arm fastening location width. Added a second fan for the FC and ESC, modified the top chassis accordingly. Added ziptie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
    [Arm - Angled.SLDPRT, Battery Case.SLDPRT, Camera ASM.SLDASM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]
2020-05-12 Added chamfers to the bottom nut capture holes to allow printing without supports. Moved the front arms further appart to better accomodate the ESC.
    [Arm - Angled.SLDPRT, Camera ASM.SLDASM, Camera Mount.SLDPRT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]
2020-06-07 Added cutout guides for the components on the main chassis. Added antenna holders for better fastening. Added propeller guards.
    [Antenna Mount.SLDPRT, Arm - Angled.SLDPRT, Buzzer.SLDPRT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]
2020-06-26 Added a servo-based undercarriage payload release mechanism.
    [Arm - Angled.SLDPRT, Battery Case.SLDPRT, Leg Long.SLDPRT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]
2020-07-04 Updated files
    [Antenna Mount.SLDPRT, Arm - Angled.SLDPRT, BMP Mount.SLDPRT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]
2020-07-10 Tested the entire system (Joystick over UDP) on the physical drone. Added attitude and other board info from FC over MSP. Changed the MSP library to YAMSPy to get MSP over USB to work. Moved everythi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
2020-07-15 Separated the code into the Dispatcher. Moved the sensor interfaces to the Modules folder.
2020-07-20 Tested the code for the Sonar. Managed to set up a wifi hotspot on the Jetson Nano for router-less connection with the Ground Station. Connection performance has improved greatly.
2020-08-12 Updated some components.
    [ALU spacer.SLDPRT, Antenna Mount.SLDPRT, Arm - Angled.SLDPRT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]
2020-08-22 Added a GPS Node
    [ESC_RACERSTART_33A_V2.IGS, ESC_RACERSTART_33A_V2.STEP, ESC_RACERSTART_33A_V2.x_t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]
2020-09-09 Added a venv for the Ground Station. Added a cover above the front fan opening.
    [Camera ASM.SLDASM, Front Opening Cover.SLDPRT, Sonar ASM.SLDASM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]
2020-11-14 Updated some hardware components. Fixed the UDP message order.
    [Leg Long.SLDPRT, Side Cover.SLDPRT, Top Chassis ASM.SLDASM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]
2020-11-14 Removed hardware and ground station from this branch
    [3S 5.2Ah LiPo.SLDPRT, 40x40x10 DC Fan.SLDPRT, ALU spacer.SLDPRT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]
2020-11-15 Added a node for sending data back to the GroundStation
2020-11-16 Updated the gitignore file for this branch. Modified the throttle to take advantage of the full stick motion.
2020-11-18 Added a Flask server that streams real-time video from the on-board PiCam to any device on the same network.
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2020-11-19 Tested out the ROSLibJS communication library. Explored adding the live video feed in a custom html page. Added the latest source files from the Jetson.
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2020-11-22 Added Material Design icons and sliders to the UI.
2020-11-22 Added a topic for publishing GPS info messages. Median filtered the ground speed and gps elevation.
2020-11-22 Added a Google Maps view that display the drone's current location. Added info about the ground clearance and elevation of the drone, as well as the GPS-measured ground speed, thus concluding (for no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
2020-11-23 Added a BMP280 sensor interface that computes the current craft altitude. Added a topic on which altitudes (relative and absolute) and the air temperature are published.
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2020-11-24 Removed the Compute Node due to high CPU usage. Fixed the GPS publisher.
    [GPSNode.py]
2020-11-25 Added rate timings for the Interceptor and Dispatcher that reduce the CPU usage by about 50%. Added a temp reading offset to account for the residual heat generated by the regulator coil.
2020-11-25 Added support for the barometer for altitude and temperature readings. Added more navbar links, currently blank.
2020-12-05 Added blurring and noise to the input images to more closely resemble the actual images taken from a RPi camera and fed those into the tiling and detection program. Experimented with smaller image ti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
2020-12-08 Performed tiled detection on input image and filtered the results. Drew bounding boxes on the final image, starting from the image tiles.
2020-12-08 Integrated the object detector into the ROS system. Modified the Computing Node to call functions from the object detector. Added a custom array for selecting camera angles.
2020-12-09 Increased the capture resolution to FHD. Moved detection to a separate thread. Added input image sharpening. Reduced the resolution of the image being sent to the Dashboard due to latency concerns.
2020-12-09 Added the latest source files from the develop_regular branch. Updated some hardware components.
    [BMP Mount.SLDPRT, Top Chassis ASM.SLDASM, Undercarriage ASM.SLDASM]
2020-12-16 Added live frame synchronisation to prevent reading a frame before it has been written.
2021-03-01 Added logic for selecting which detection image to save from previous results. Added saving results to CSV.
    [01Mar21.csv]
2021-04-21 Added a top status bar showing the current detection results on the dashboard. Removed the other pages for now.
2021-04-21 Added the changes from the development branch.
    [Top Chassis ASM.SLDASM, Undercarriage ASM.SLDASM]
